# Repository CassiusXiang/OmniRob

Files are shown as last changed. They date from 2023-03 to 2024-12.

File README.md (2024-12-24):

# OmniRob





OmniRob is an omnidirectional mobile robot based on Mecanum wheels.

Featuring a modular design, the chassis supports four expansion modules. In this project, two modules are installed: a 4-way infrared sensor module and a material dispensing module.

## Introduction

This project originated from a course I took in the first semester of my freshman year: Design and Construction.

The course required us to design a vehicle that could both follow a track and dispense materials. Similar to traditional line-following cars, this vehicle runs along black lines on a white surface. The difference is that we also needed to equip it with a material storage and dispensing device, allowing the vehicle to accurately dispense objects at intersections on the track.

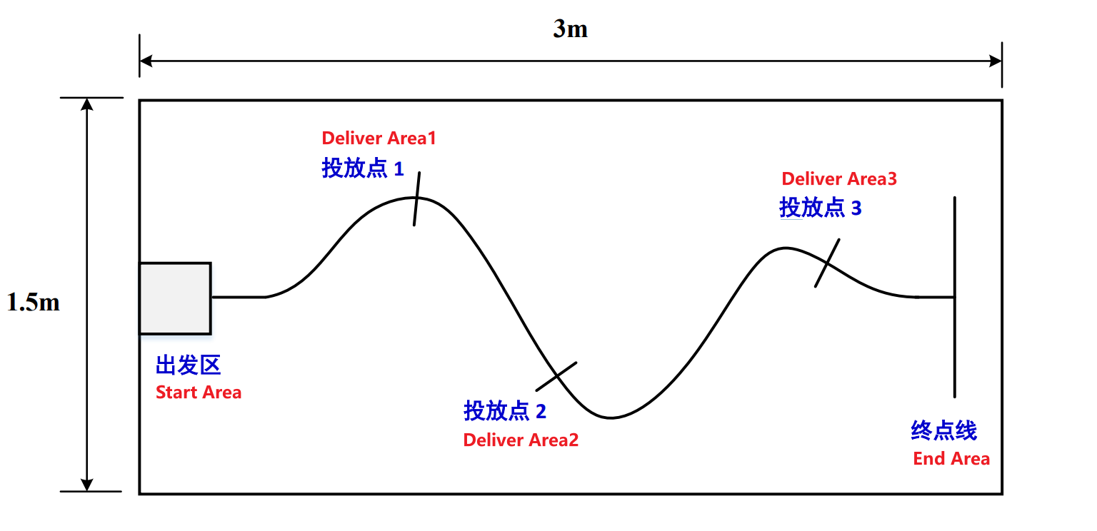
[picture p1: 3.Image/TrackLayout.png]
Track Layout


Thus, the OmniRob open-source project was born. It is an open-source, low-cost, easy-to-assemble, modularly designed Mecanum wheel robot. It uses four DC brushed motors with encoders, controlled by an Arduino. To drive the motors, I also designed a motor driver Shield board for the Arduino, which will be discussed later.

The top and front/back of the vehicle have four modular interfaces for installing different modules. We installed a 4-way infrared sensor at the front and a material storage and dispensing device driven by a servo motor at the top.

OmniRob

## Components

1. 3D-printed chassis, top cover, dispensing mechanism
2. 4 MG513 DC gear motors, gear ratio 1:30
3. 4 Mecanum wheels with a diameter of 65mm
4. Several M2.5 screws
5. MG996R servo motor
6. Arduino UNO
7. Custom 4-motor driver Shield (directly plugs into the Uno)
8. 12V lithium battery
9. 4-way infrared sensors

**Total Cost ~\$40**

For installation and internal structure, see the [Installation Guide](https://github.com/CassiusXiang/OmniRob/blob/main/Installation.md).

## Motor Driver Shield - MUNO

The motor driver Shield uses a 2-layer PCB design, created with Altium Designer 2022.

The driver board uses four AS4950 chips to drive the motors, with a maximum driving current of up to 2A per channel.

The designed Shield board can be directly inserted into the Arduino UNO, as shown in the image 4.

<div style="display: flex; justify-content: space-around; flex-wrap: wrap;">
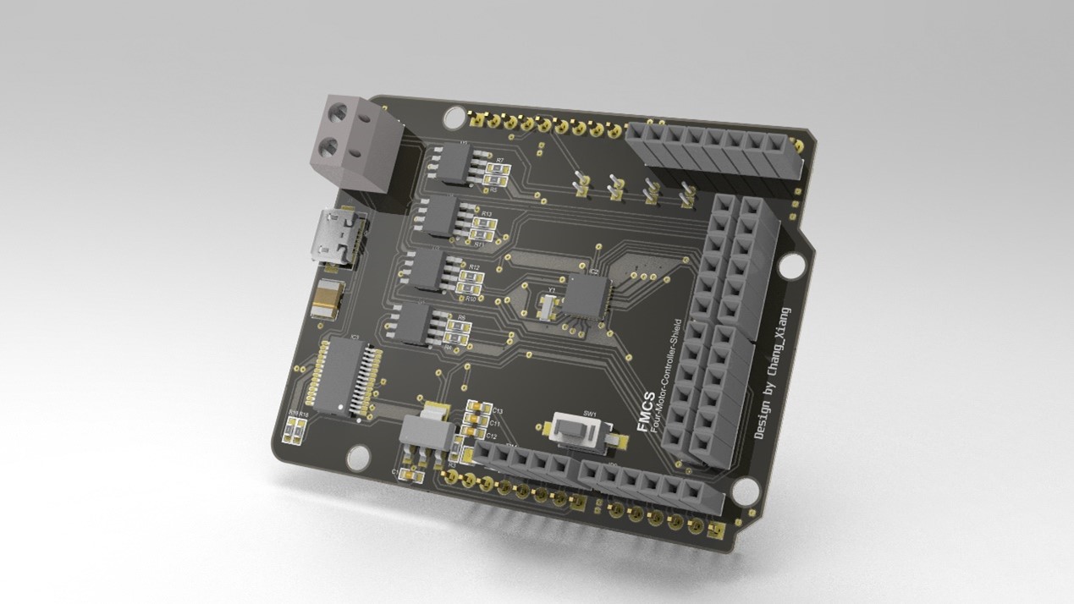
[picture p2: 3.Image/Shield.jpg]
    
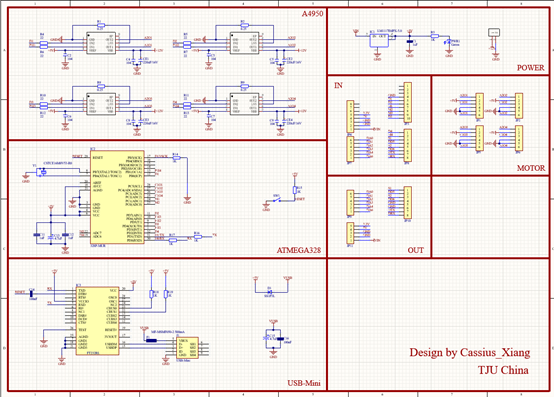
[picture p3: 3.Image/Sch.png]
    
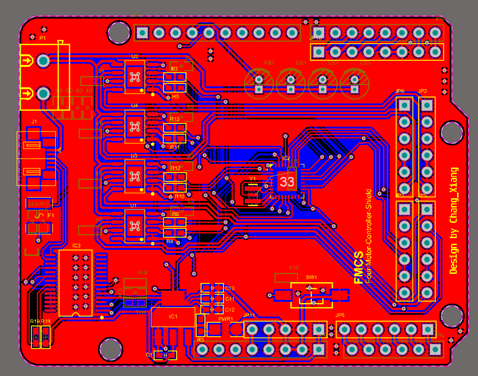
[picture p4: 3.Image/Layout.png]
    
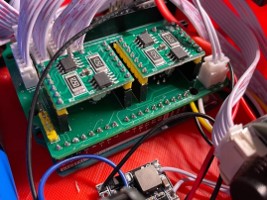
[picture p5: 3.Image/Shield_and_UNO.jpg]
    
</div>

## Dispensing Mechanism

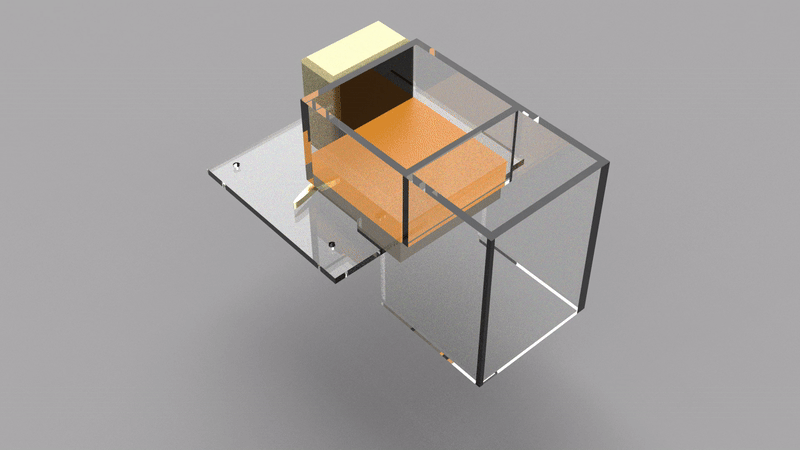
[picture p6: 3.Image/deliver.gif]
Dispensing Mechanism


## Video Demonstration

[Watch the Video](https://www.youtube.com/watch?v=084VByHCzTs)

## Installation and Usage

Refer to the [Installation Guide](https://github.com/CassiusXiang/OmniRob/blob/main/Installation.md).

## License

OmniRob is released under the MIT License. Please refer to the [LICENSE](https://github.com/CassiusXiang/OmniRob/blob/main/LICENSE) file for more information.

## Contact

My email: changxiangchina@outlook.com

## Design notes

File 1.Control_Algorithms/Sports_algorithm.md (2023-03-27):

Mecanum Wheels
==============

Existing Research
-----------------

*   Domestic research institutions (Southeast University, Shanghai University, Harbin Institute of Technology, Zhejiang University)
*   Wang Yizhi analyzed and established the kinematic model of Mecanum four-wheel system
*   A.Gfrerrer derived an accurate kinematic model considering stick shape
*   G.Campion et al. derived the three-dimensional motion equation using matrix transformation
*   Patrick F.Muir et al. established the kinematic model considering wheel slippage
*   K.Nagatan et al. proposed a visual pose calculation algorithm considering wheel slippage
*   L.Gracia et al. derived the kinematic model considering wheel slippage using the method of successive approximation for robot dynamics.

Kinematic Forward and Inverse Solution Algorithms for Mecanum Four-Wheel Systems
--------------------------------------------------------------------------------

<aside> 💡 Based on ideal conditions </aside>

The motion of the vehicle can be expressed by the following three quantities:

$$
（\dot{x},\dot{y},\omega)
$$

We can control the speed of four motors:

$$
（\omega_1,\omega_2,\omega_3,\omega_4)
$$

To control the motion.
These two vectors are converted using the matrix $B$:

$$
\begin{bmatrix}
\omega_1\\
\omega_2\\
\omega_3\\
\omega_4\\
\end{bmatrix}
=B\cdot
\begin{bmatrix}
\dot{x}\\
\dot{y}\\
\omega\\
\end{bmatrix}
$$

<p align="center">
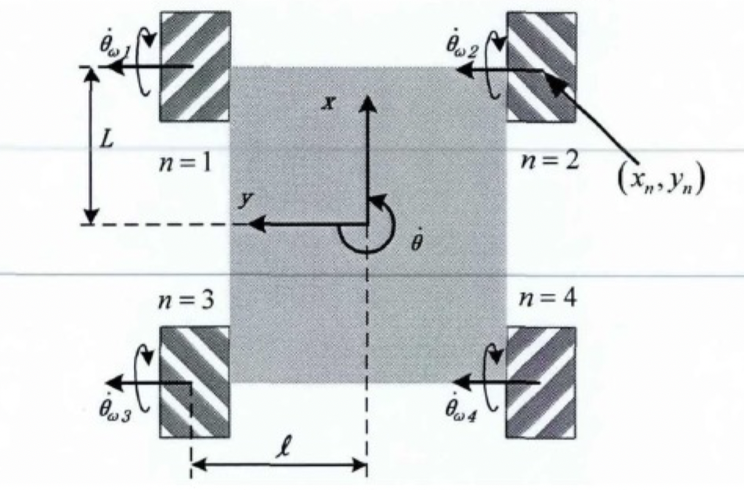
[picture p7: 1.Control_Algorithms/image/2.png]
Description of image
  
</p>

The above figure shows the layout diagram of the Mecanum wheels used in this project.

Thanks to the work of G.Campion et al., we can directly obtain the inverse matrix $B$:

$$
B=\frac{1}{R}
\begin{bmatrix}
1&-1&-L-l\\
1&1&L+l\\
1&1&-L-l\\
1&-1&L+l\\
\end{bmatrix}
$$

Dynamic Modeling of Mecanum Wheels
----------------------------------

Definition: $m$ is the total mass of the vehicle, $J\_z$ and $J\_r$ are the moments of inertia of the vehicle around the $z$ axis and the wheels, respectively.

The Lagrangian method is used to perform dynamic modeling:

Potential energy:

$$
V=0
$$

Kinetic energy:

$$
K=\frac{1}{2}m(\dot{x}^2+\dot{y}^2)+\frac{1}{2}J_z\omega^2+\frac{1}{2}J_r\sum_{i=1}^{4}{\omega_i^2}
$$

Using the Lagrange equation:

$$
\frac{d}{dt}(\frac{\partial K}{\partial \omega_i})-\frac{\partial K}{\partial \theta_i}=T_i
$$

Solve for $(\\dot{x},\\dot{y},w)$:

$$
{T}={M\cdot\ddot{\theta}}+{D\cdot\dot{\theta}}
$$

where:

$$
T=(T_1,T_2,T_3,T_4)^T;
\theta=(\theta_1,\theta_2,\theta_3,\theta_4)^T;
D=diag(D_1,D_2,D_3,D_4)
$$

$T$ is the output torque of the motor, and $D$ is the coefficient matrix related to friction. The matrix $M$ is defined as:

$$
M=
\begin{bmatrix}
C&-B&B&D\\
-B&C&B&D\\
B&D&C&-B\\
D&B&-B&C 
\end{bmatrix}
;
A=\frac{mR^2}{8};
B=\frac{J_zR^2}{16(L+l)^2};
C=A+B+J_r;
D=A-B
$$

In subsequent algorithm design, the influence of torque $T$ should be considered.

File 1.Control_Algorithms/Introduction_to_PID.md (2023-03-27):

Introduction to PID
===================

$$
PID\=P+I+D
$$

Meaning of PID Controller
-------------------------

PID controller (proportional-integral-derivative controller) consists of proportional unit, integral unit, and derivative unit. The characteristics of the controller can be adjusted by adjusting the gains of these three units. The PID controller calculates the error based on the input data and reference value and adjusts the new input value based on historical data to make the system reach or maintain the reference value.

PID can be reduced to PI, PD, P, and I controllers by reducing the control parameters.

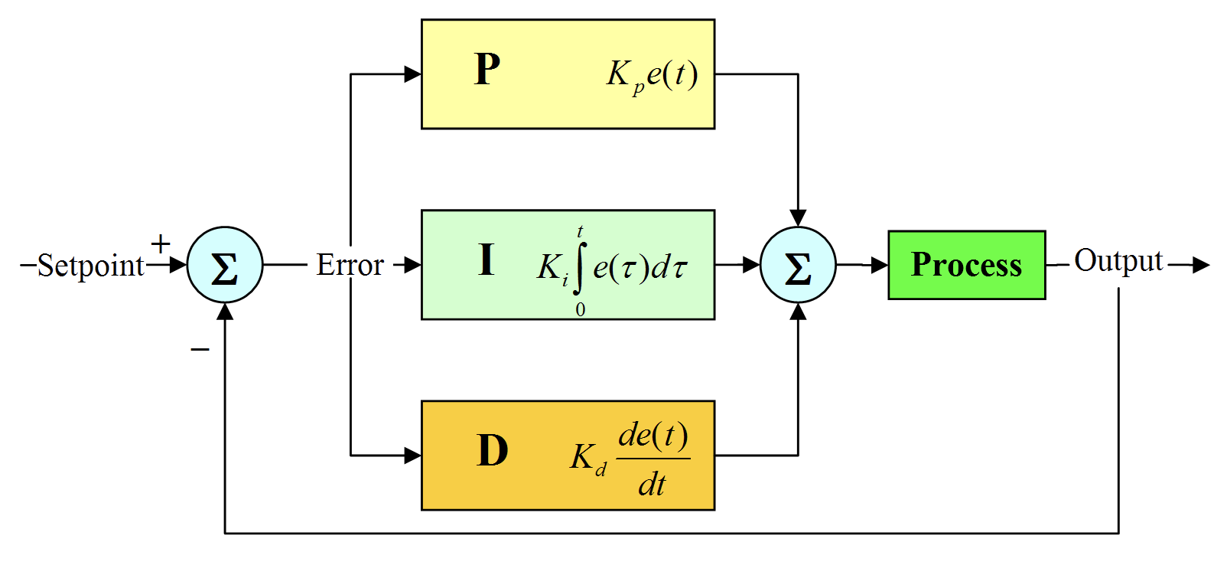
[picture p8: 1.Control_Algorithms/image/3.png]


Figure 1. Block diagram of the control loop of a PID controller

Theory
------

The PID algorithm can be expressed as follows:

$$
u(t)=K_pe(t)+K_i\int_0^te(\tau)d\tau+K_d\frac{d}{dt}e(t)
$$

Where:

$K$: Proportional gain (tuning parameter)

$e$: Error = Setpoint - Feedback

$t$: Current time

$\tau$: Integration variable

The transfer function in the transfer equation $Y(s)=H(s)X(s)$ is:

$$
H(s)=\frac{K_ds^2+K_ps+K_i}{s+C}
$$

Component Analysis
------------------

### Proportional Unit (P)

Proportional control considers the current error, which is multiplied by the error value and a positive constant $K\_p$ (representing proportionality).

For example, for controlling a kettle, it can be represented as:

$$
P_{out}=K_Pe(t)
$$

where $e(t)$ is the difference between the current temperature and the target temperature (positive), and the control effect curve is shown below:

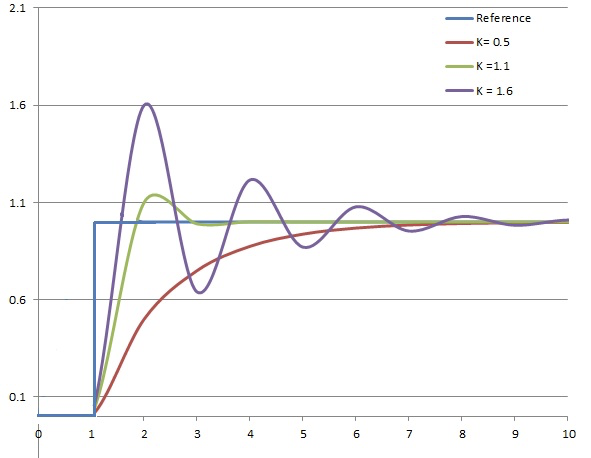
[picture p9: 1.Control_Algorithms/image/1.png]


### Integral Unit (I)

The integral unit considers the total historical error.

It is used to eliminate the bias that exists from the beginning of the system to the present. The integral control term is as follows:

$$
I_{out}=K_i\int_0^te(\tau)d\tau
$$

### Derivative Unit (D)

The derivative unit considers future possible errors.

For example, when controlling a particle to maintain its position at $x=0$, once $\\dot{x}$ is not zero, although there is no error at this time, it means that an error will occur soon, and the derivative unit will react immediately to achieve control.

The differential control term is as follows:

$$
D_{out}=K_d\frac{d}{dt}e(t)
$$

Parameter Tuning
----------------

### Two Types of Systems

1.  Linear system

For general linear systems, the gain value generally does not change, and multiple simulation simulations are usually required in the design until the final control result achieves satisfactory results.

2.  Nonlinear system

For nonlinear systems, an algorithm may be needed to control the variable parameters (gain planning algorithm correction).

### Tuning Methods

It can be divided into four types:

1.  Manual tuning
2.  Ziegler-Nichols method
3.  Software debugging
4.  Cohen-Coon

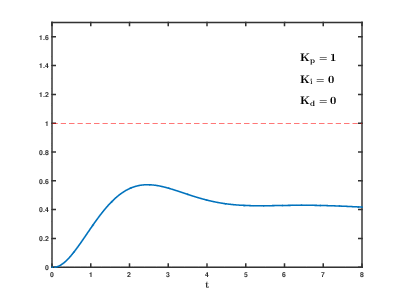
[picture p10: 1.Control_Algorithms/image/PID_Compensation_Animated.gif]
PID


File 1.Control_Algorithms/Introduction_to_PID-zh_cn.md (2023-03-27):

# Introduction to PID

$$
PID=P+I+d
$$

## PID控制器的含义

PID控制器（比例-积分-微分控制器），由由比例单元、积分单元、微分单元组成。可以通过调整这三个单元的增益来调整其特性。PID控制器根据输入的数据和参考值来计算误差，同时根据历史数据来调整新的输入值，目的是为了使系统达到或保持在参考值。

PID可以减少控制参数，从而变成PI、PD、P、I控制器。

图1.PID控制器的控制回路方块图

图1.PID控制器的控制回路方块图

## 理论

PID算法可以用下式表示：

$$
u(t)=K_pe(t)+K_i\int_0^te(\tau)d\tau+K_d\frac{d}{dt}e(t)
$$

其中：

$K$：为比例增益（调适参数）

$e$：误差 = 设定值 - 回授值

$t$：目前时间

$\tau$：积分变量

传递方程 $Y(s)=H(s)X(s)$ 中的传递函数为：

$$
H(s)=\frac{K_ds^2+K_ps+K_i}{s+C}
$$

## 控件分析

### 比例单元（；）

比例控制考虑当前误差，误差值和一个正值的常数$K_p$（表示比例）相乘

例如对于一个热水壶的控制，可以用如下式子来表示：

$$
P_{out}=K_Pe(t)
$$

其中：$e(t)$为目前温度与目标温度的差值（正值），控制效果曲线如下



### 积分单元（Integral）

积分单元考虑历史总误差

用于消除从系统开始到现在所存在的偏差，这容易理解，积分控制的项如下：

$$
I_{out}=K_i\int_0^te(\tau)d\tau
$$

### 微分单元（Derivative）

微分单元考虑未来可能的误差

比如控制一个质点保持在$x=0$的位置，那么$\dot{x}$一旦不为0，虽然此时并未有任何误差产生，但是这意味着马上就会产生误差，此时微分单元将会马上做出反应，以实现控制。

微分控制的项如下：

$$
D_{out}=K_d\frac{d}{dt}e(t)
$$

## 参数调试

### 两种系统

1. 线性系统

对于一般的线性系统，增益的取值一般不会发生改变，在设计时一般要经过多次的仿真模拟，直到最终的控制结果实现令人满意的效果。

1. 非线性系统

对于非线性系统，可能需要一套算法来控制可变参数（增益规划算法修正）

### 调试方法

可以分为四种：

1. 人工调试
2. 齐格勒－尼科尔斯方法
3. 软件调试
4. Cohen-Coon

PID的调参过程

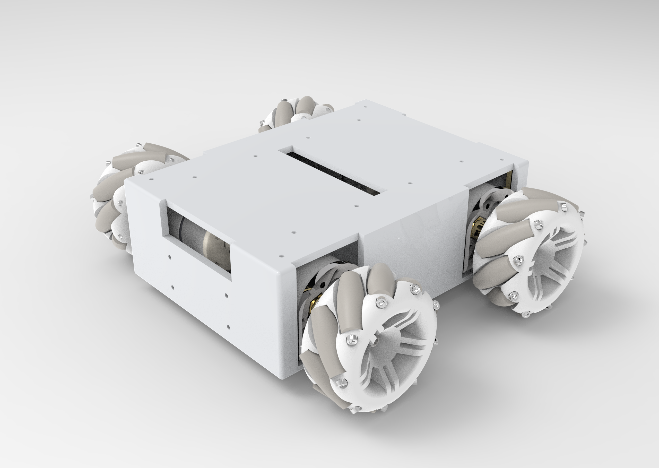
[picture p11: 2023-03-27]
1.Control_Algorithms/image/main.4.png

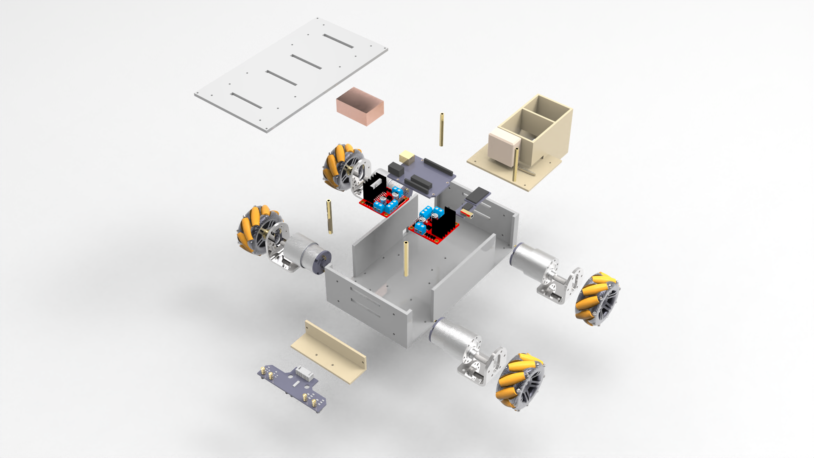
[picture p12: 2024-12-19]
3.Image/ExplodedView.png

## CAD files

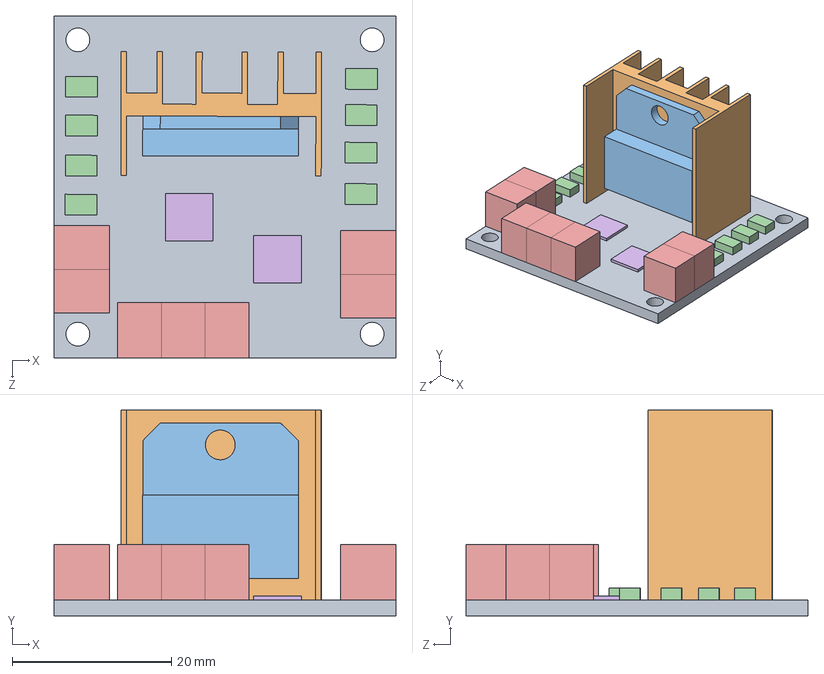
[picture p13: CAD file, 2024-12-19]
0.Model/SolidworksFiles/L298N_sim.SLDASM
43.0 x 25.9 x 43.0 mm
电机底板
散热片替代品
芯片替代品
小黑块 x 8
大蓝块 x 7
圆柱底板 x 2

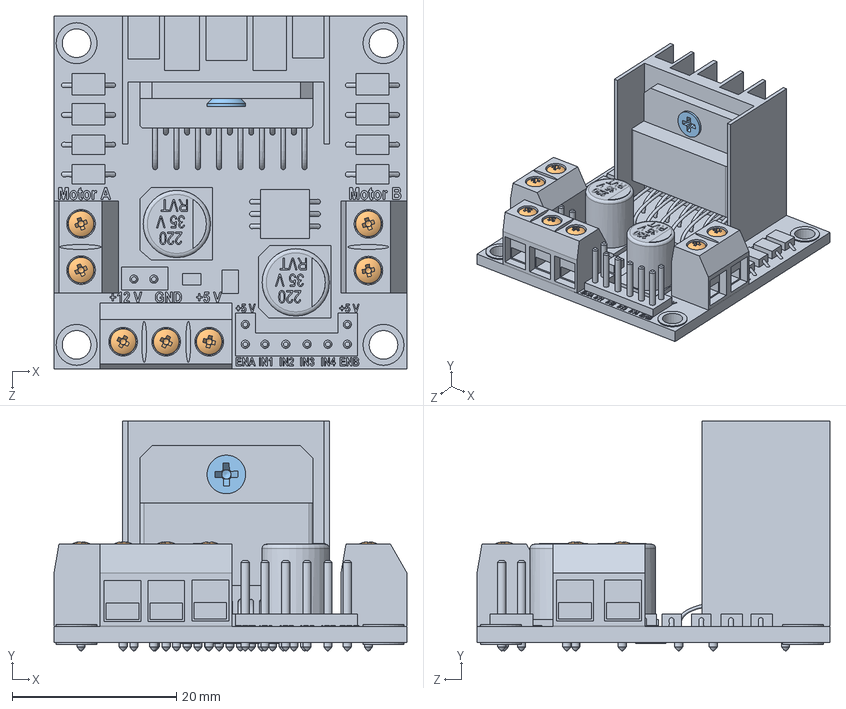
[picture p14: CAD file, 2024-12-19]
0.Model/SolidworksFiles/L298N Stepper Motor Driver (Red).SLDASM
43.0 x 28.0 x 43.0 mm
L298N Stepper Motor Driver (Red)
pan head cross recess screw_iso x 7
countersunk flat head cross recess screw_iso

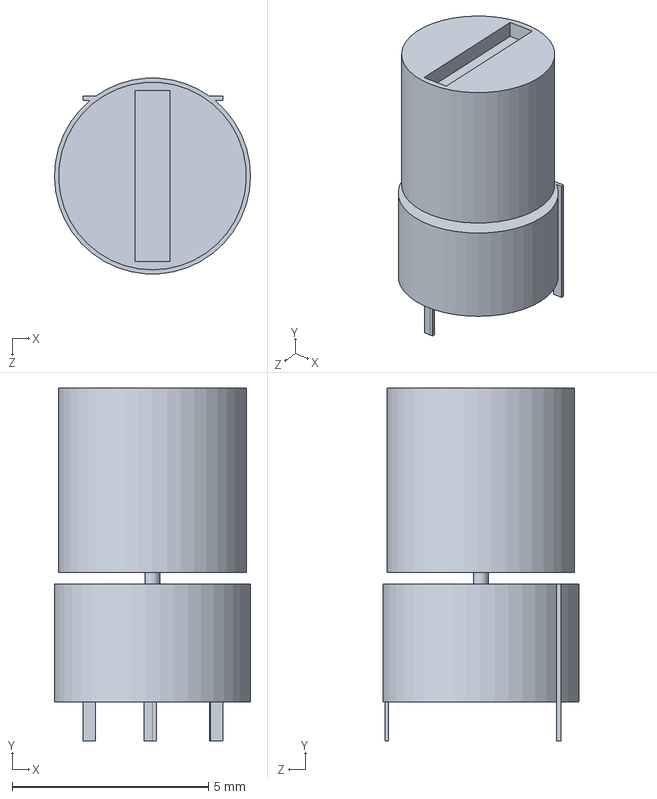
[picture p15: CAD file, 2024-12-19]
0.Model/SolidworksFiles/圆柱.SLDPRT
5.00 x 9.00 x 4.99 mm

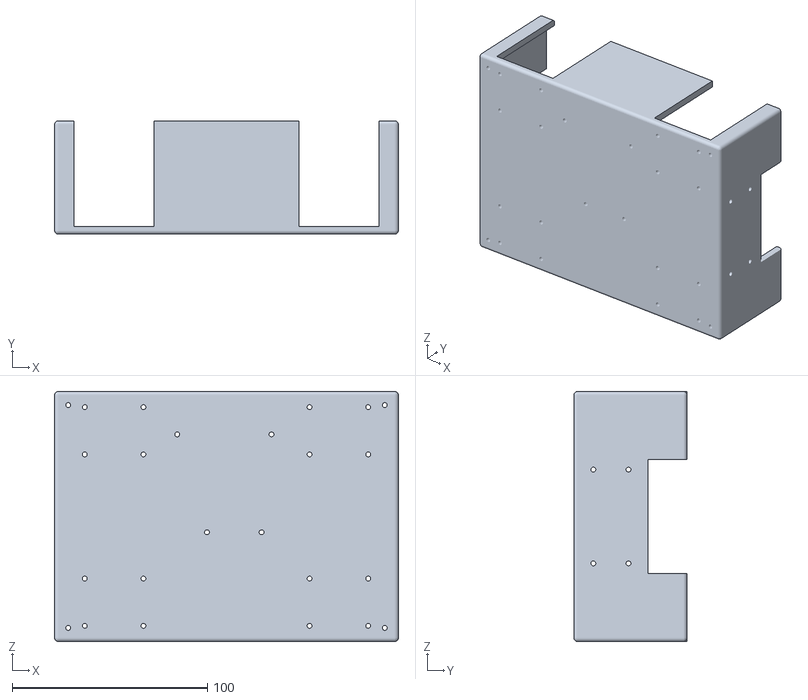
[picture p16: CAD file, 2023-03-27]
0.Model/STL/Bottom.STL
176.0 x 58.0 x 128.0

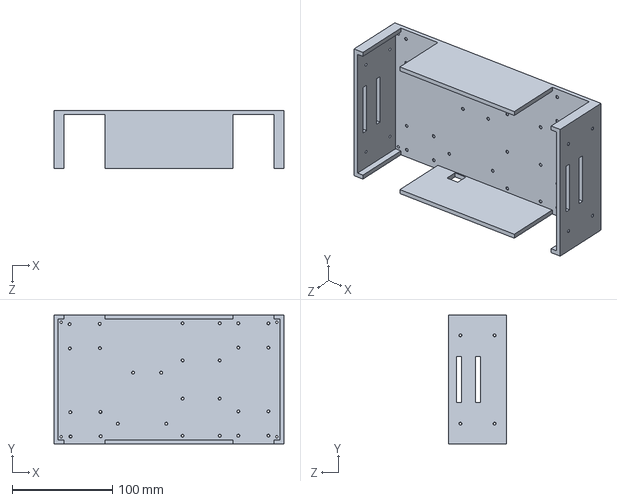
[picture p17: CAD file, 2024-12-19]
0.Model/SolidworksFiles/整车设计(下部).SLDPRT
229.0 x 128.0 x 58.0 mm

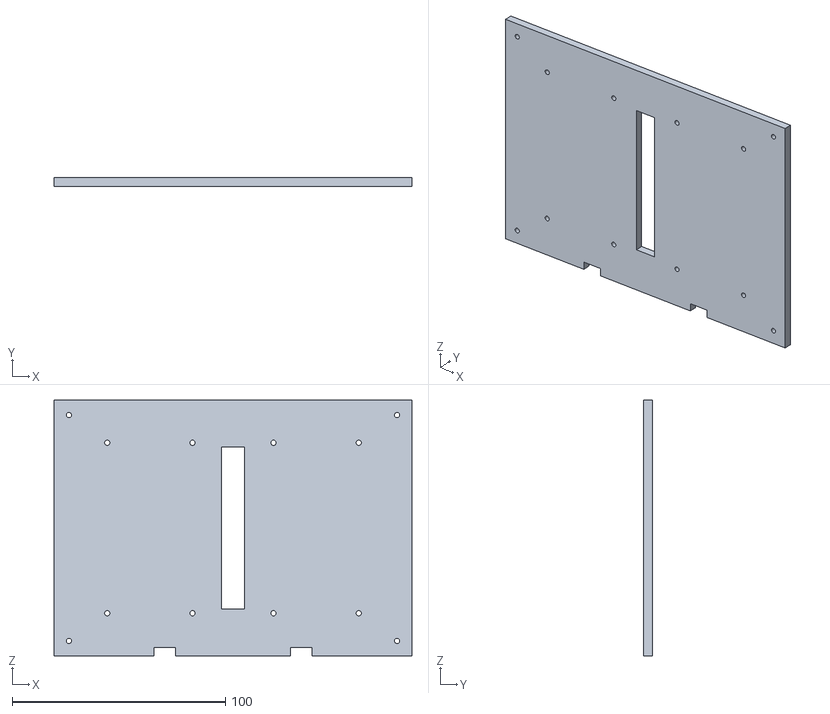
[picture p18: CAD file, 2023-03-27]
0.Model/STL/Upper.STL
168.0 x 4.00 x 120.0

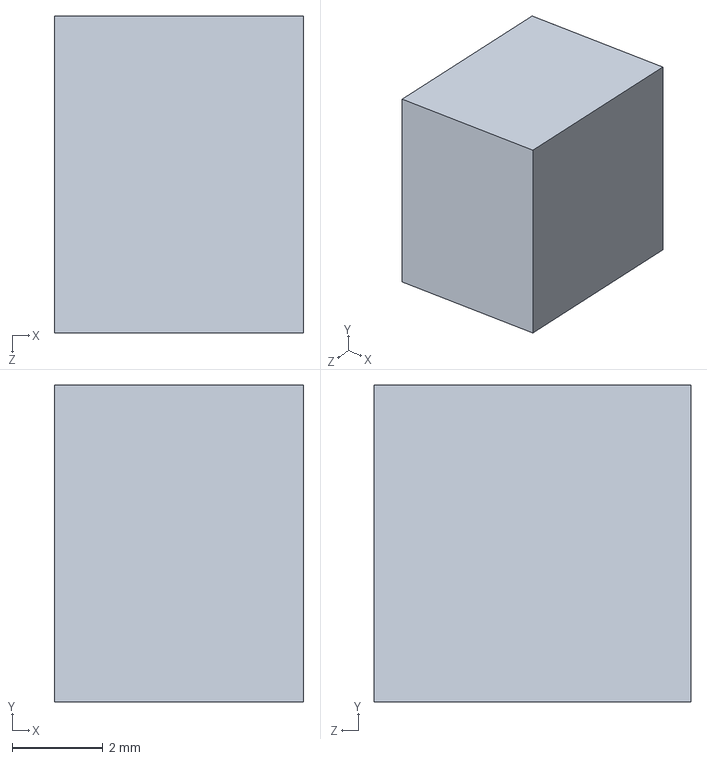
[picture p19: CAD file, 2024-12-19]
0.Model/SolidworksFiles/大蓝块.SLDPRT
5.50 x 7.00 x 7.00 mm

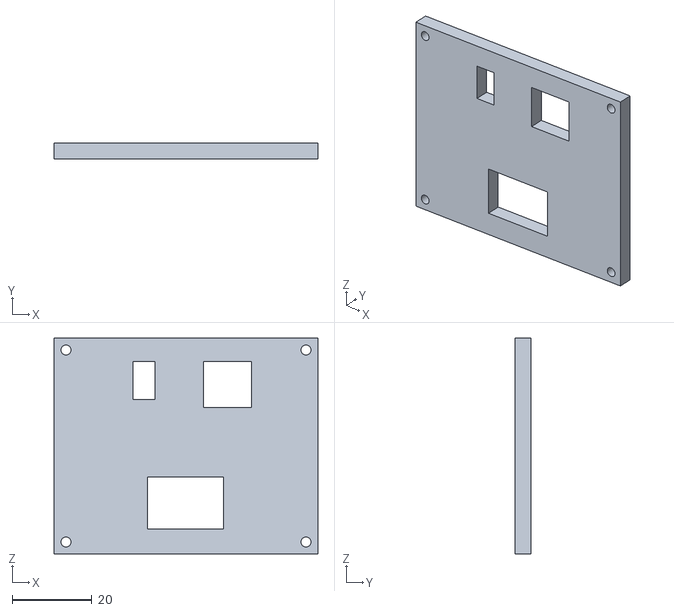
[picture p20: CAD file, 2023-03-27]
0.Model/STL/Side Panel.STL
66.0 x 4.00 x 54.0

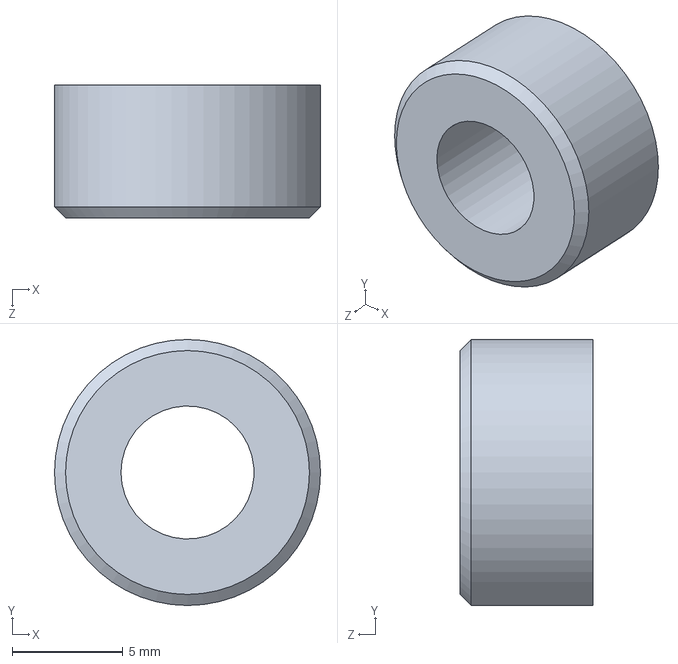
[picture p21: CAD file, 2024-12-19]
0.Model/SolidworksFiles/SHAFT COUPLER, JGB37-520.SLDPRT
12.0 x 12.0 x 6.00 mm

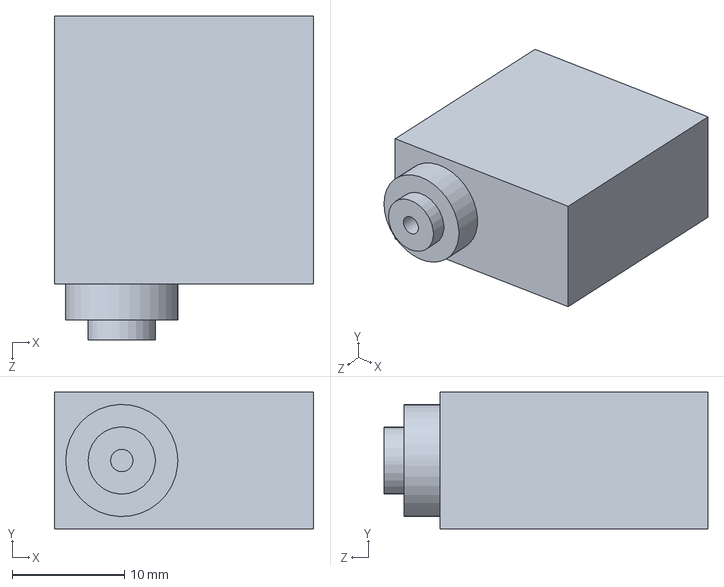
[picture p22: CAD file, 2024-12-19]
0.Model/SolidworksFiles/180度舵机.SLDPRT
23.1 x 12.2 x 28.9 mm

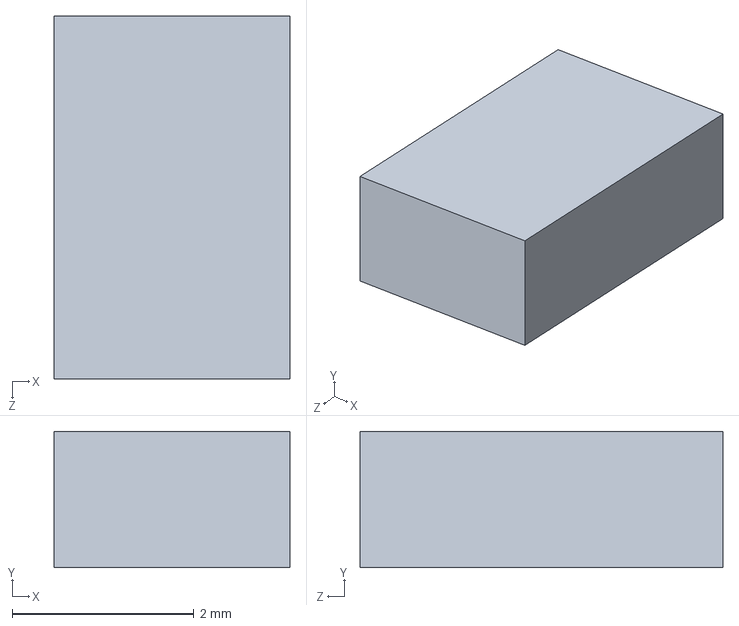
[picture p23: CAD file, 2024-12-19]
0.Model/SolidworksFiles/小黑块.SLDPRT
2.60 x 1.50 x 4.00 mm

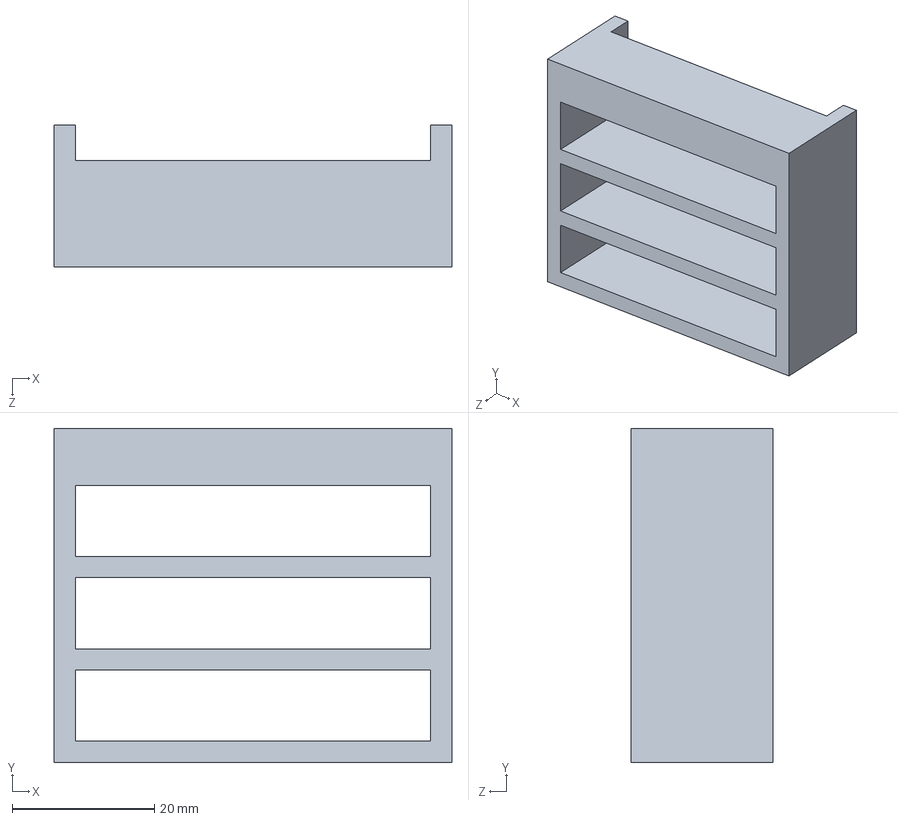
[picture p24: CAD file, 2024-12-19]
0.Model/SolidworksFiles/推块.SLDPRT
56.0 x 47.0 x 20.0 mm

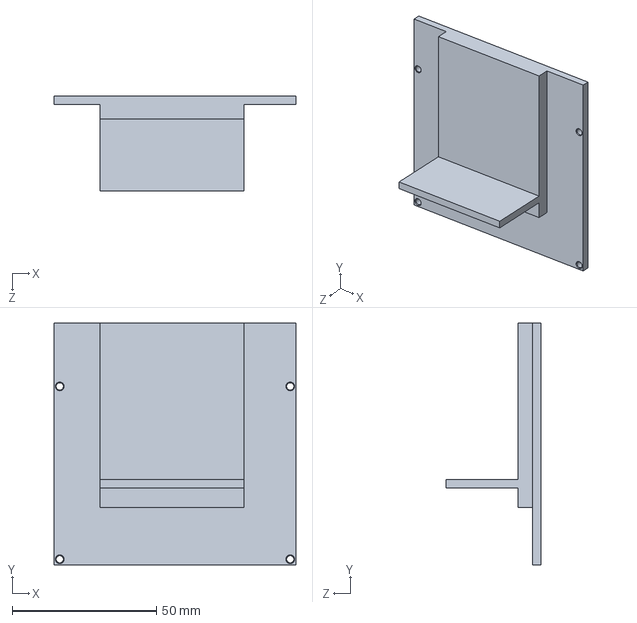
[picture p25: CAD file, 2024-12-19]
0.Model/SolidworksFiles/外壳.SLDPRT
84.0 x 84.0 x 33.0 mm

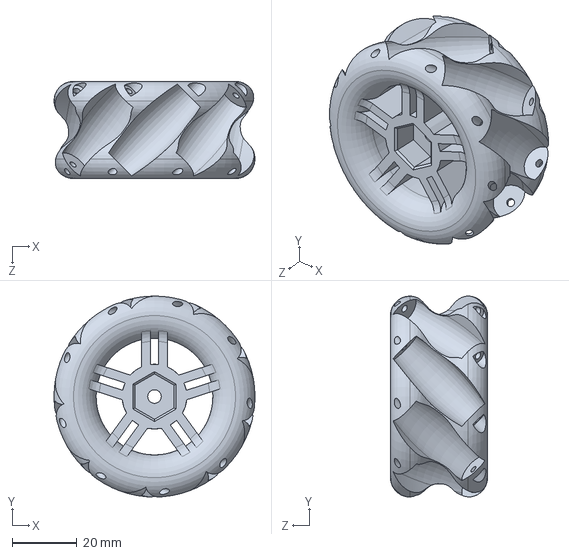
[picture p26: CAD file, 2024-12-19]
0.Model/SolidworksFiles/65mm右旋轮毂.SLDPRT
62.0 x 62.0 x 30.0 mm

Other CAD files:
0.Model/SolidworksFiles/销螺栓.SLDPRT
0.Model/SolidworksFiles/新底板.SLDPRT
0.Model/SolidworksFiles/轴.SLDPRT
0.Model/SolidworksFiles/投放模块2.SLDPRT
0.Model/SolidworksFiles/65mm左旋轮毂.SLDPRT
0.Model/SolidworksFiles/ArduinoUNO.SLDPRT
0.Model/SolidworksFiles/CONNECTION, DC MOTOR, JGB37-520.SLDPRT
0.Model/SolidworksFiles/COUPLING BRACKET, GEARED BODY TO DC MOTOR, JGB37-520.SLDPRT
0.Model/SolidworksFiles/DC MOTOR, JGB37-520.SLDPRT
0.Model/SolidworksFiles/DC16.8V.SLDPRT
0.Model/SolidworksFiles/GEARED BODY, MOTOR, JGB37-520.SLDPRT
0.Model/SolidworksFiles/JGB37-520 12 v metal geared motor bracket.SLDPRT
0.Model/SolidworksFiles/L298N Stepper Motor Driver (Red).SLDPRT
0.Model/SolidworksFiles/MOTOR SHAFT, JGB37-520.SLDPRT
0.Model/SolidworksFiles/PLASTIC COVER, DC MOTOR, JGB37-520.SLDPRT
0.Model/SolidworksFiles/上板.SLDPRT
0.Model/SolidworksFiles/主体 - 副本.SLDPRT
0.Model/SolidworksFiles/主体.SLDPRT
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

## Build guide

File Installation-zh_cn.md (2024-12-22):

安装说明
=============




硬件要求
----

*   Arduino UNO控制板
*   Arduino 扩展板
*   供电板
*   4个麦卡纳姆轮
*   2个电机驱动板
*   4个JGB37-520直流电机
*   3D打印好的主体模型
*   蓝牙模块（可选）
*   12V电池或其他合适的电源
*   杜邦线、螺丝等小配件

软件要求
----

*   Arduino IDE

安装步骤
----

1. **下载代码**

   在[main.ino](https://github.com/CassiusXiang/OmniRob/tree/main/Software/main)下载麦卡纳姆轮智能小车代码。

2. **连接硬件**

   将Arduino UNO控制板插入电脑，使用杜邦线连接直流电机以及其他扩展模块。

3. **打开Arduino IDE**

   打开Arduino IDE软件，将代码文件打开。点击"Tools"->"Board"，选择"Arduino Uno"作为板子。

4. **上传代码**

   点击"Sketch"->"Upload"上传代码。

5. **控制小车**

   打开蓝牙串口调试助手，在设备列表中找到蓝牙模块并连接。在调试助手中输入命令，就可以控制小车前进、后退、左转、右转等动作。

实物样例
----

组装完成的实物图：



接线示意图：



注意事项
----

*   在安装过程中，请仔细阅读代码中的注释，并正确连接硬件。
*   使用蓝牙串口调试助手时，请确保设备列表中已找到蓝牙模块并连接成功。
*   在控制小车时，请注意安全。不要将小车放在不平衡或易倾斜的表面上，以免发生意外。
*   请参考实物图进行安装，注意麦卡纳姆轮的方向
*   接线请参考接线示意图

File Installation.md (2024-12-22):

Installation Instructions
=========================




Hardware Requirements
---------------------

*   Arduino UNO control board
*   Arduino expansion board
*   Power supply board
*   4 Mecanum wheels
*   2 motor driver boards
*   4 JGB37-520 DC motors
*   3D printed main body model
*   Bluetooth module (optional)
*   12V battery or other suitable power supply
*   Dupont wires, screws, and other small accessories

Software Requirements
---------------------

*   Arduino IDE

Installation Steps
------------------

1. **Download the code**

   Download the Mecanum wheel intelligent small car code from [main.ino](https://github.com/CassiusXiang/OmniRob/tree/main/Software/main).

2. **Connect the hardware**

   Insert the Arduino UNO control board into the computer and use Dupont wires to connect the DC motors and other expansion modules.

3. **Open Arduino IDE**

   Open the Arduino IDE software and open the code file. Click "Tools"->"Board" and select "Arduino Uno" as the board.

4. **Upload the code**

   Click "Sketch"->"Upload" to upload the code.

5. **Control**

   Open the Bluetooth serial debugging assistant, find and connect to the Bluetooth module in the device list. Enter commands in the debugging assistant to control the small car to move forward, backward, turn left, turn right, and other actions.

Physical Sample
---------------

Picture of the assembled physical sample:



Wiring diagram:



Precautions
-----------

*   During the installation process, please read the comments in the code carefully and connect the hardware correctly.
*   When using the Bluetooth serial debugging assistant, please make sure that the Bluetooth module has been found and connected successfully in the device list.
*   When controlling the small car, please pay attention to safety. Do not place the small car on an unbalanced or easily tilted surface to avoid accidents.
*   Please refer to the physical sample for installation and pay attention to the direction of the Mecanum wheels.
*   Please refer to the wiring diagram for wiring.

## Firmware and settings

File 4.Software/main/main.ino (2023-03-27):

//by @Xiang Chang
const int sensor1 = A0;
const int sensor2 = A1;
const int sensor3 = A2;
const int sensor4 = A3;

const int en1 = 6; const int D1 = 4;
const int en2 = 9; const int D2 = 7;
const int en3 = 10; const int D3 = 8; 
const int en4 = 11; const int D4 = 12;

int sensor[4] = {0, 0, 0, 0};
const float Kp_2 = 58, Ki_2 = 0.008, Kd_2 = 15;
const float vc = 90;
float PID_2 = 0;
float error = 0;
float P = 0, I = 0, D = 0, p_error = 0;
float v1 = 0, v2 = 0, v3 = 0, v4 = 0;

void setup(){
  pinMode(sensor1, INPUT);
  pinMode(sensor2, INPUT);
  pinMode(sensor3, INPUT);
  pinMode(sensor4, INPUT);
  pinMode(D1, OUTPUT);  pinMode(D2, OUTPUT);  pinMode(D3, OUTPUT);  pinMode(D4, OUTPUT);
  pinMode(en1, OUTPUT);  pinMode(en2, OUTPUT);  pinMode(en3, OUTPUT);  pinMode(en4, OUTPUT);
}

void L1_f(float v) {
  digitalWrite(D1, HIGH); 
  analogWrite(en1, v);
}
void L1_b(float v) {
  digitalWrite(D1, LOW); 
  analogWrite(en1, v);
}
void L2_f(float v) {
  digitalWrite(D2, LOW); 
  analogWrite(9, v);
}
void L2_b(float v) {
  digitalWrite(D2, HIGH); 
  analogWrite(9, v);
}
void L3_f(float v) {
  digitalWrite(D3, LOW); 
  analogWrite(en3, v);
}
void L3_b(float v) {
  digitalWrite(D3, HIGH); 
  analogWrite(en3, v);
}
void L4_f(float v) {
  digitalWrite(D4, HIGH); 
  analogWrite(en4, v);
}
void L4_b(float v) {
  digitalWrite(D4, LOW); 
  analogWrite(en4, v);
}

void L1(float v) {
  if(v > 0) 
    L1_f(255-v);
  else 
    L1_b(-v);
}
void L2(float v) {
  if(v > 0) 
    L2_f(v);
  else 
    L2_b(225+v);
}
void L3(float v) {
  if(v > 0) 
    L3_f(v);
  else 
    L3_b(255+v);
}
void L4(float v) {
  if(v > 0) 
    L4_f(255-v);
  else 
    L4_b(-v);
}

void loop(){

  sensor[0] = digitalRead(sensor1);
  sensor[1] = digitalRead(sensor2);
  sensor[2] = digitalRead(sensor3);
  sensor[3] = digitalRead(sensor4);

  if(sensor[1] != 0 && sensor[0] == 0 && sensor[2] == 0 && sensor[3] != 0)
    error = 0;
  else if(sensor[1] == 0 && sensor[0] != 0 && sensor[2] != 0 && sensor[3] != 0)
    error = -1.3;
  else if(sensor[1] != 0 && sensor[0] == 0 && sensor[2] != 0 && sensor[3] != 0)
    error = -1;
  else if(sensor[1] != 0 && sensor[0] != 0 && sensor[2] == 0 && sensor[3] != 0)
    error = 1;
  else if(sensor[1] != 0 && sensor[0] != 0 && sensor[2] != 0 && sensor[3] == 0)
    error = 1.3;

//PID Control
  P = error;
  I = I + error;
  D = error - p_error;
  PID_2 = Kp_2 * P + Ki_2 * I + Kd_2 * D;
  p_error = error;

//change v
  v1 = vc + PID_2;
  v2 = vc - PID_2;
  v3 = vc + PID_2;
  v4 = vc - PID_2;
//constrain
  constrain(v1, -255, 255);
  constrain(v2, -255, 255);
  constrain(v3, -255, 255);
  constrain(v4, -255, 255);

  L1(v1);L2(v2);L3(v3);L4(v4);
}

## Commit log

2023-03-27 Create Introduction to PID-zh_cn
2023-03-27 Update Introduction to PID-zh_cn
2023-03-27 Rename Introduction to PID-zh_cn to Introduction to PID-zh_cn.md
2023-03-27 Update Introduction to PID-zh_cn.md
2023-03-27 Create Introduction to PID.md
2023-03-27 Update Introduction to PID.md
